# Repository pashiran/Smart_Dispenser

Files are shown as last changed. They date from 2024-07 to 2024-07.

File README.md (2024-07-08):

Smart Dispenser for MAKERS

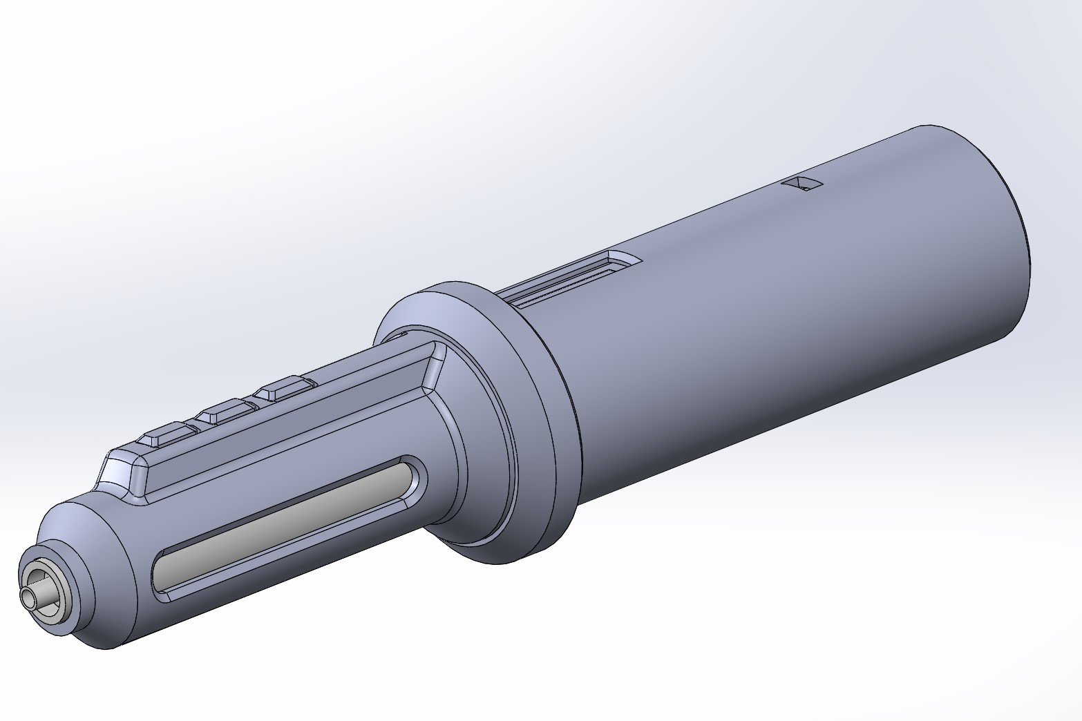
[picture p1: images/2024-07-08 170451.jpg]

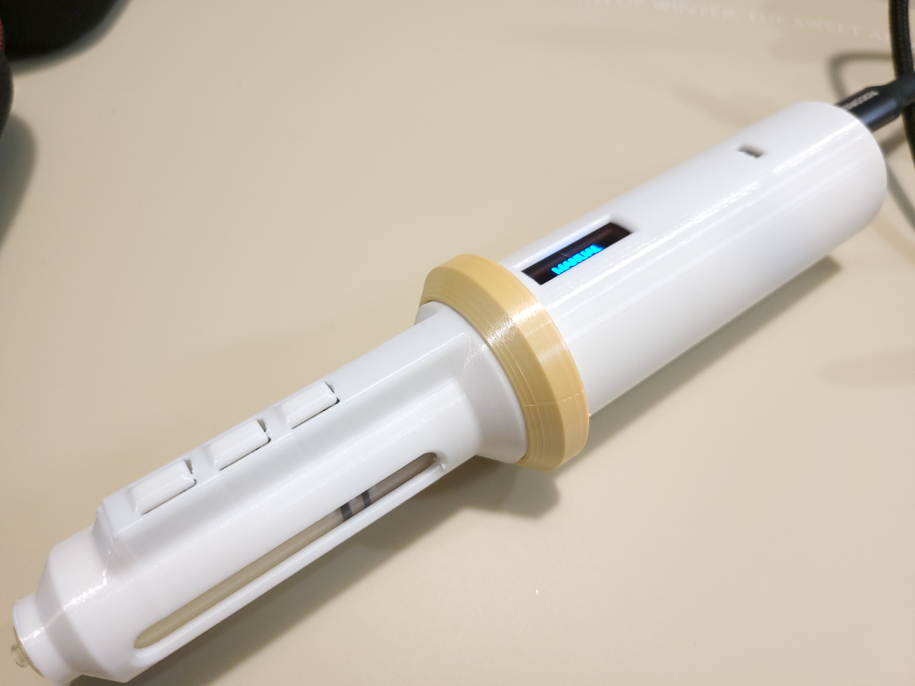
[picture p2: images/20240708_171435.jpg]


When you're building electronic circuits, some tools are so industrial that they're rarely useful for personal use. 
Instead of a giant pneumatic dispenser that sits on your desk, I created a USB-powered dispenser that fits in the palm of your hand. 

It took me a lot of time to build the hardware, electronics, and software all by myself. 
I'm not a professional programmer, so the software is waiting for other people to make it better.

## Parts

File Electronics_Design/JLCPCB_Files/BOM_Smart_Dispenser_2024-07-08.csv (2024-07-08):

ID | Name | Designator | Footprint | Quantity | Manufacturer Part | Manufacturer | Supplier | Supplier Part | Price
1 | TYPE-C-31-M-12 | USBC1 | USB-C_SMD-TYPE-C-31-M-12 | 1 | TYPE-C-31-M-12 | 韩国韩荣 | LCSC | C165948 | 0.163
2 | 5.1kΩ | R1 | R0805 | 1 | 0805W8F1002T5E | UNI-ROYAL(厚声) | LCSC | C17414 | 0.002
3 | 22pF | C1,C2 | C0805 | 2 | CL21C220JBANNNC | SAMSUNG(三星) | LCSC | C1804 | 0.01
4 | 4.7u | C10,C12,C16 | C0805 | 3
5 | 100nF | C11,C4,C3 | C0805 | 3 | C0805B104K500NT | TORCH(火炬) | LCSC | C476766 | 0.003
6 | 2.2u | C13 | C0805 | 1
7 | 1u | C14,C15 | C0805 | 2
8 | 0.1u | C17,C18 | C0805 | 2
9 | 100uF | C5 | CAP-D6.3×H5.5 | 1
10 | 4.7k | R6,R7,R8 | R0805 | 3
11 | 910k | R9 | R0805 | 1
12 | DRV8833PWP | U3 | TSSOP-16_L5.0-W4.4-P0.65-LS6.4-BL-EP | 1 | DRV8833PWPR | TI(德州仪器) | LCSC | C50506 | 0.639
13 | 1N5819 | U4 | SOD-123_L2.7-W1.6-LS3.7-FD | 1 | 1N5819W | HXY MOSFET(华轩阳电子) | LCSC | C5451628 | 0.006
14 | LM1117S-5.0 | U5 | SOT-223-3_L6.5-W3.4-P2.30-LS7.0-BR | 1 |  | HTC | LCSC | C126028 | 0.165
15 | 5.1kΩ | R10,R11 | R0805 | 2 | 0805W8F1001T5E | UNI-ROYAL(厚声) | LCSC | C17513 | 0.002
16 | 1kΩ | R12,R2,R3,R4 | R0805 | 4 | 0805W8F1001T5E | UNI-ROYAL(厚声) | LCSC | C17513 | 0.002
17 | LED-0603_R | LED1 | LED0603_RED | 1 | 19-217/R6C-AL1M2VY/3T | EVERLIGHT(台湾亿光) | LCSC | C72044 | 0.018
18 | TS-1101-C-W | RESET,SW1,SW2,SW3 | SW-SMD_L6.0-W3.3-LS8.0 | 4 | TS-1101-C-W | XKB Connectivity(中国星坤) | LCSC | C318938 | 0.033
19 | ATMEGA328P-AU | U1 | TQFP-32_L7.0-W7.0-P0.80-LS9.0-BL | 1 | ATMEGA328P-AU | MICROCHIP(美国微芯) | LCSC | C14877 | 2.131
20 | 0.1uF | C6 | C0805 | 1 | C0805B104K500NT | TORCH(火炬) | LCSC | C476766 | 0.003
21 | 10nF | C7 | C0805 | 1 | C0805B104K500NT | TORCH(火炬) | LCSC | C476766 | 0.003
22 | 2.2uF | C8 | C0805 | 1 | CL21A226MAYNNNE | SAMSUNG(三星) | LCSC | C602037 | 0.021
23 | 22uF | C9 | C0805 | 1 | CL21C222JBFNNNE | SAMSUNG(三星) | LCSC | C28260 | 0.029
24 | HDR-M-2.54_2x3 | J1 | HDR-M-2.54_2X3 | 1 |  |  | LCSC | C65114 | 0.029
25 | HDR-M-2.54_1x6 | J2 | HDR-M-2.54_1X6 | 1 |  |  | LCSC | C190819 | 0.029
26 | SC662K-3.3V | LDO1 | SOT-23-3_L2.9-W1.3-P1.90-LS2.4-BR | 1 | SC662K-3.3V | FM(富满) | LCSC | C83932 | 0.034
27 | CH340K | U2 | ESOP-10_L4.9-W3.9-P1.00-LS6.2-BL-EP | 1 | CH340K | WCH(南京沁恒) | LCSC | C968586 | 0.629
28 | SSD1306_OLED | U6 | 0.91"OLED_FOLD | 1
29 | 16MHZ | Y1 | X3-SMD-3.6X1.3X0.8MM | 1 | CSTCE16M00G55-RO |  | SeeedStudio | 306010053
30 | 10kΩ | R5 | R0805 | 1 | 0805W8F1002T5E | UNI-ROYAL(厚声) | LCSC | C17414 | 0.002

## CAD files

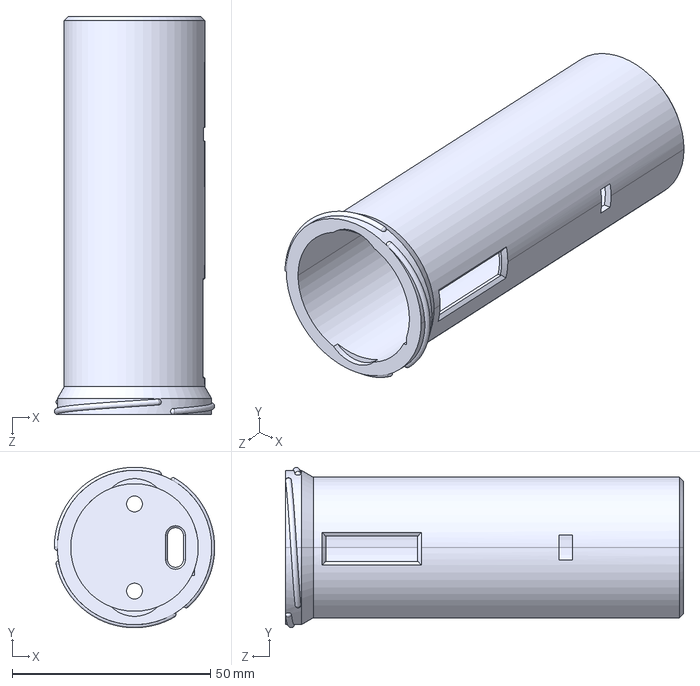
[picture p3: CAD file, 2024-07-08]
3D_Cad/STEP/Main_Body_Cover.STEP
40.5 x 40.5 x 100.5 mm

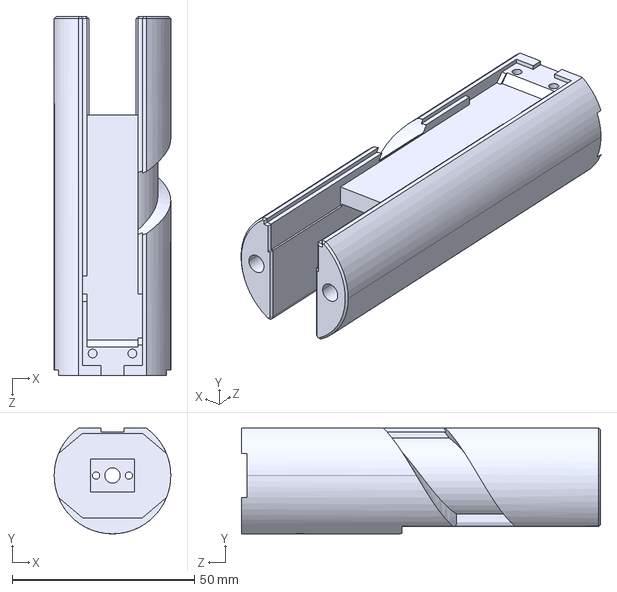
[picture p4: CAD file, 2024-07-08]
3D_Cad/STEP/Main_Body.STEP
32.0 x 29.0 x 98.5 mm

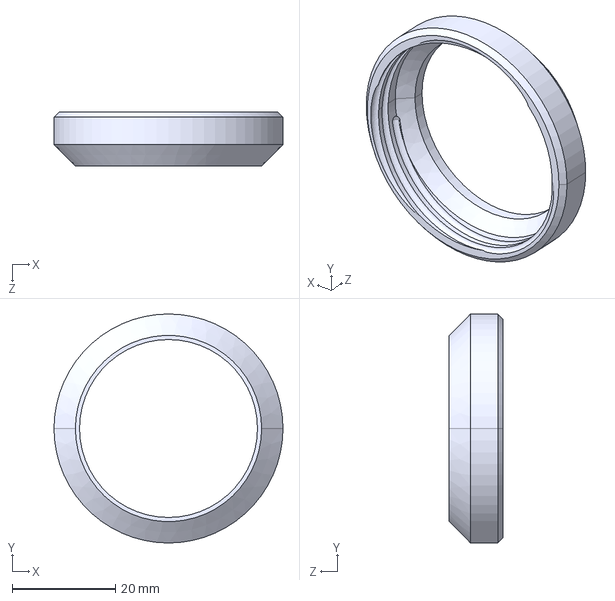
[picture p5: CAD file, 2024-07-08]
3D_Cad/STEP/Joint_Handle.STEP
44.4 x 44.4 x 10.5 mm

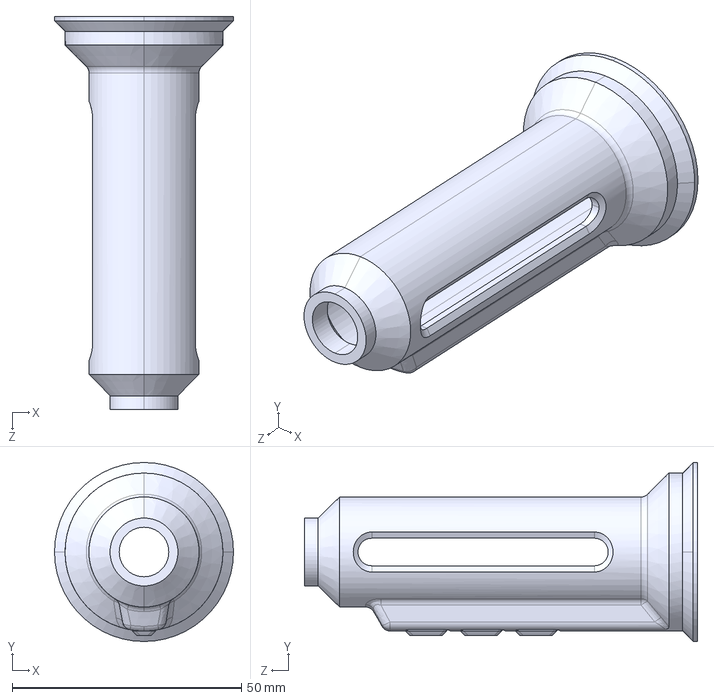
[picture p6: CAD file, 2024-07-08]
3D_Cad/STEP/Front_Body.STEP
39.0 x 39.0 x 85.7 mm

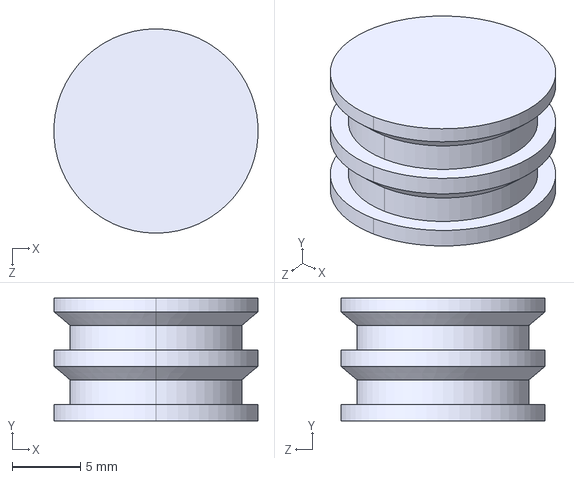
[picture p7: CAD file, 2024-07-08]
3D_Cad/STEP/Pusher_A.STEP
15.0 x 9.00 x 15.0 mm

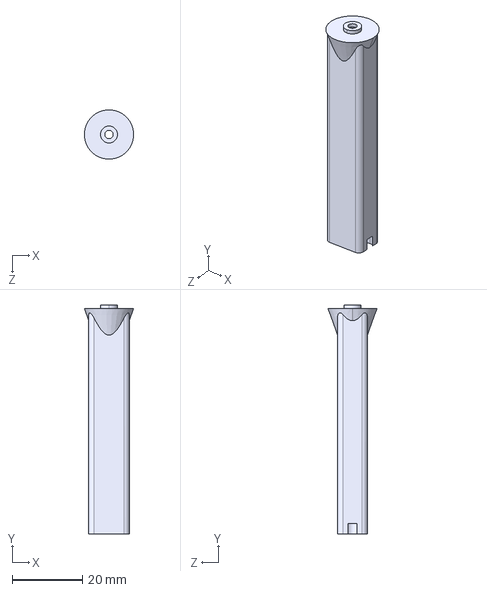
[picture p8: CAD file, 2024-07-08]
3D_Cad/STEP/Pusher_B.STEP
14.0 x 65.0 x 14.0 mm

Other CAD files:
3D_Cad/STL/Front_Body.STL
3D_Cad/STL/Joint_Handle.STL
3D_Cad/STL/Main_Body.STL
3D_Cad/STL/Main_Body_Cover.STL
3D_Cad/STL/Pusher_A.STL
3D_Cad/STL/Pusher_B.STL

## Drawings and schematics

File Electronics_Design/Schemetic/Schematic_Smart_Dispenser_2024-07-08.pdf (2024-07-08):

## Input A1: Voltage

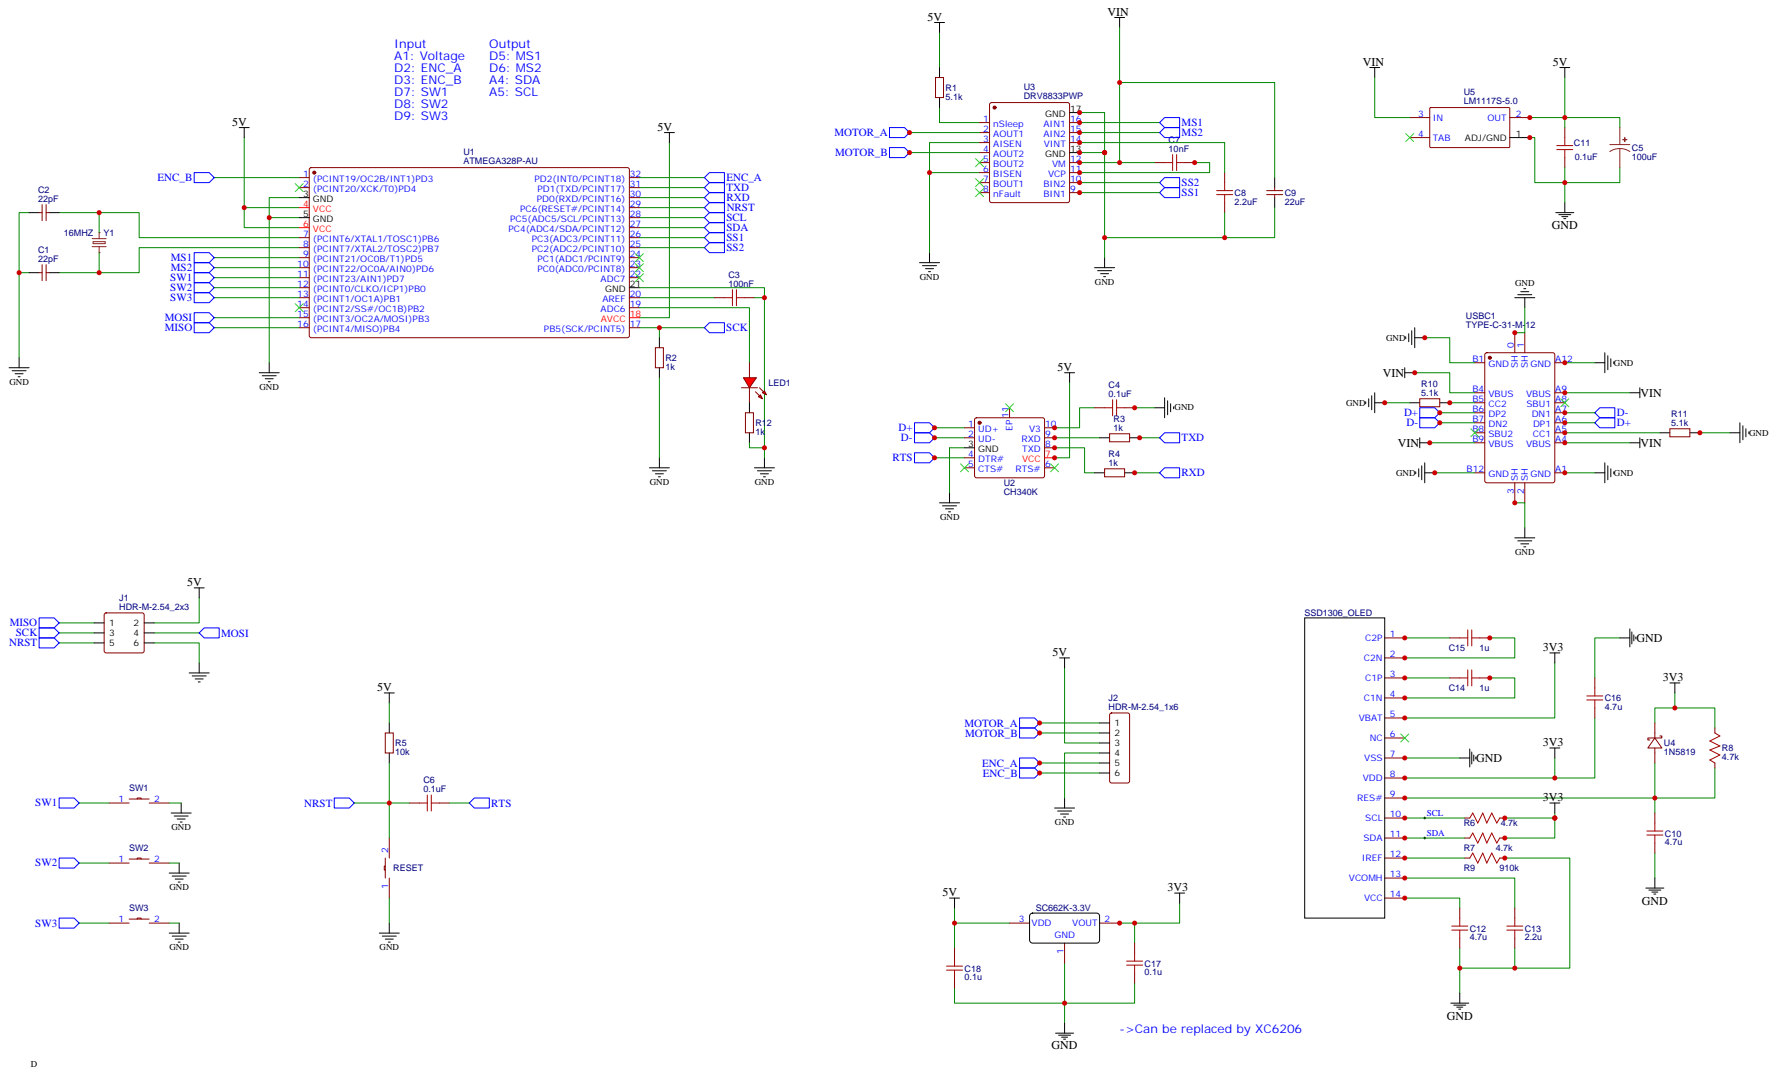
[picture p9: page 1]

->Can be replaced by XC6206

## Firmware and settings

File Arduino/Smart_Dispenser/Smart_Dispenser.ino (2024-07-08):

#include "U8glib.h"
#include "EEPROM.h"
#include "Encoder.h"  // https://github.com/PaulStoffregen/Encoder


// 핀 정의
#define encoderA 2  // pin of motor encoder - interrupt of arduino nano
#define encoderB 3  // pin of motor encoder - interrupt of arduino nano
#define up_Pin 7    // Up switch
#define sel_Pin 8   // Select switch
#define down_Pin 9  // Down switch
//#define limit_Pin 10  // Limit sensor

#define AIN_Pin_1 5  // drv8833 signal 1 : PWM
#define AIN_Pin_2 6  // drv8833 signal 2 : PWM

// 전역 변수
long newPosition;
long oldPosition;    // encoder position
boolean direction;   // true = cylinder advance, false = cylinder retraction
int min_error = 30;  // encoder difference less than this number will be ignored

long currentPos;  // cylinder first(=current) position
long targetPos;   // cylinder position to move
long difference;  // difference of currentPos and targetPos

boolean up_Flag = false, select_Flag = false, down_Flag = false;  // switch flag

byte address;  // EEPROM address (0:stage, 1:Extrusion, 2:Retraction, 3:Speed)
byte Stage = 0, previous_Stage = 0;  // 0 = manual, 1 = auto, 2 = PnP, 4 = Setup
byte setup_Stage = 0;        // setup stage, 0 = extrusion, 1 = retraction, 2 = speed
byte Extrusion;              // extrusion set amount.(min:0 / max:100), maximum extrusion moves the cylinder 5mm
byte Retraction;             // retraction set amount.(min:0 / max:10), maximum retraction moves the cylinder 1mm
int Speed;                   // speed of motor(min: -255 / max :255), minus means direction
byte Backlash;               // backlash
float Pitch = 0.4;           // pitch of M4 bolt.
int gearRatio = 50;          // gear ratio of geared motor.
byte X, Y;                   // coordinate of OLED screen

unsigned long current_Millis, previous_Millis = 0;  // Time variable to check the time the switch is pressed
unsigned long pressed_Time = 500;  // Time-based variable. If it is longer than this, it is considered as a LONG press.


long initialPosition;            // PnP 모드에서 엔코더의 현재 위치 저장 변수


U8GLIB_SSD1306_128X32 u8g(U8G_I2C_OPT_FAST);  // I2C / TWI
Encoder myEncoder(encoderA, encoderB);

void setup() {
  pinMode(up_Pin, INPUT_PULLUP);
  pinMode(sel_Pin, INPUT_PULLUP);
  pinMode(down_Pin, INPUT_PULLUP);
  pinMode(encoderA, INPUT_PULLUP);
  pinMode(encoderB, INPUT_PULLUP);

  pinMode(AIN_Pin_1, OUTPUT);
  pinMode(AIN_Pin_2, OUTPUT);

  u8g.setFont(u8g_font_helvB10);

  u8g.setFontRefHeightExtendedText();
  u8g.setDefaultForegroundColor();
  u8g.setFontPosTop();

  Serial.begin(9600);
  Serial.println("OK");

  if (EEPROM.read(0) == 255) {  // if there are no saved settings
    Extrusion = 10;             // use default value
    Retraction = 1;
    Speed = 255;
    // 초기화 완료 표시를 위해 임의의 값을 EEPROM의 첫 번째 위치에 기록
    EEPROM.write(0, 0);
    EEPROM.write(1, Extrusion);
    EEPROM.write(2, Retraction);
    EEPROM.write(3, Speed);
  } else {
    Extrusion = EEPROM.read(1);
    Retraction = EEPROM.read(2);
    Speed = EEPROM.read(3);
  }

  draw();
}

void loop() {
  newPosition = myEncoder.read();
  current_Millis = millis();

  // Stage에 따른 동작 처리
  switch (Stage) {
    case 0:  // manual stage
      // 스위치 상태 읽기
      if(digitalRead(up_Pin) == LOW) {
        digitalWrite(AIN_Pin_1, Speed);
        digitalWrite(AIN_Pin_2, LOW);
      }
      if(digitalRead(down_Pin) == LOW) {
        digitalWrite(AIN_Pin_1, LOW);
        digitalWrite(AIN_Pin_2, Speed);
      }
      if((digitalRead(up_Pin) == HIGH) && (digitalRead(down_Pin) == HIGH)){
        stopMotor();
      }
      
      // sel 스위치 처리 함수 호출
      handleSelSwitch();
      break;

    case 1:  // auto stage
      // up 스위치를 누르면 - extrusion 거리 만큼 전진한 뒤 retraction 거리만큼 후진하고 멈춘다.
      if (!up_Flag && digitalRead(up_Pin) == LOW) {
        up_Flag = true;
      } else if (up_Flag && digitalRead(up_Pin) == HIGH) {
        up_Flag = false;
        moveMotor(Extrusion);
        moveMotor(-Retraction);
        stopMotor();
      }

      // down 스위치를 눌렀다 떼면 - extrusion 거리 만큼 후진하고 멈춘다.
      if (!down_Flag && digitalRead(down_Pin) == LOW) {
        down_Flag = true;
      } else if (down_Flag && digitalRead(down_Pin) == HIGH) {
        down_Flag = false;
        moveMotor(-Extrusion);
        stopMotor();
      }

      // sel 스위치를 처리 함수 호출
      handleSelSwitch();
      break;

    case 2:  // Pick and Place stage
      // up 스위치를 누르면 - 스위치를 누른 동안 계속 후진하다가 스위치를 떼면 다시 현재 위치까지 돌아오고 멈춘다.
      if (!up_Flag && digitalRead(up_Pin) == LOW) {
        up_Flag = true;
        initialPosition = myEncoder.read();  // 현재 위치 저장
      } else if (up_Flag && digitalRead(up_Pin) == LOW) {
        // 스위치가 눌린 동안 계속 후진
        digitalWrite(AIN_Pin_1, LOW);
        analogWrite(AIN_Pin_2, Speed);
      } else if (up_Flag && digitalRead(up_Pin) == HIGH) {
        // 스위치가 떼지면 최대 속도로 기존의 위치로 돌아옴
        up_Flag = false;
        long target = initialPosition;
        while (newPosition != target) {
          newPosition = myEncoder.read();
          if (newPosition < target) {
            analogWrite(AIN_Pin_1, 255);  // 최대 속도로 전진
            digitalWrite(AIN_Pin_2, LOW);
          } else {
            digitalWrite(AIN_Pin_1, LOW);
            analogWrite(AIN_Pin_2, 255);  // 최대 속도로 후진
          }
        }
        stopMotor();
      }

      // sel 스위치를 처리 함수 호출
      handleSelSwitch();
      break;

    case 4:  // setup stage
      // up 스위치 상태 읽기
      if (!up_Flag && digitalRead(up_Pin) == LOW) {
        up_Flag = true;
        if (setup_Stage == 0 && Extrusion < 100) {
          Extrusion++;
          draw(); // 화면 업데이트
        } else if (setup_Stage == 1 && Retraction < 10) {
          Retraction++;
          draw(); // 화면 업데이트
        } else if (setup_Stage == 2) {
          if (Speed < 255) {
            Speed += 26;  // 0~255 범위에서 10단계로 변하기 위해
            if (Speed > 255) Speed = 255;
            draw(); // 화면 업데이트
          }
        }
      } else if (up_Flag && digitalRead(up_Pin) == HIGH) {
        up_Flag = false;
      }

      // down 스위치 상태 읽기
      if (!down_Flag && digitalRead(down_Pin) == LOW) {
        down_Flag = true;
        if (setup_Stage == 0 && Extrusion > 0) {
          Extrusion--;
          draw(); // 화면 업데이트
        } else if (setup_Stage == 1 && Retraction > 0) {
          Retraction--;
          draw(); // 화면 업데이트
        } else if (setup_Stage == 2) {
          if (Speed > 0) {
            Speed -= 26;  // 0~255 범위에서 10단계로 변하기 위해
            if (Speed < 0) Speed = 0;
            draw(); // 화면 업데이트
          }
        }
      } else if (down_Flag && digitalRead(down_Pin) == HIGH) {
        down_Flag = false;
      }

      // sel 스위치를 처리 함수 호출
      handleSelSwitch();
      break;

  }

  // 위치 변경 시 OLED 화면 업데이트
  if (newPosition != oldPosition) {
    oldPosition = newPosition;
    draw();
  }
}

void stopMotor() {
    digitalWrite(AIN_Pin_1, HIGH);
  digitalWrite(AIN_Pin_2, HIGH);
}

// 모터를 지정된 거리만큼 이동시키는 함수
void moveMotor(int distance) {
  // 이동할 거리를 엔코더 신호 수로 변환
  int counts = (distance * 12 * gearRatio) / Pitch;
  long target = newPosition + counts;

  while (newPosition != target) {
    newPosition = myEncoder.read();
    if (counts > 0) {
      digitalWrite(AIN_Pin_1, Speed);
      digitalWrite(AIN_Pin_2, LOW);
    } else {
      digitalWrite(AIN_Pin_1, LOW);
      digitalWrite(AIN_Pin_2, Speed);
    }
  }
}

// sel 스위치 입력 처리 함수
void handleSelSwitch() {
  if (!select_Flag && digitalRead(sel_Pin) == LOW) {
    select_Flag = true;
    previous_Millis = current_Millis;  // 버튼을 누른 시간 저장
  } else if (select_Flag && digitalRead(sel_Pin) == HIGH) {
    unsigned long pressDuration = current_Millis - previous_Millis;

    if (pressDuration < pressed_Time) {
      // Short press: Stage 변경 또는 setup_Stage 순환
      if (Stage == 4) {
        setup_Stage = (setup_Stage + 1) % 3; // setup stage 순환
      } else {
        Stage = (Stage + 1) % 3; // 0, 1, 2 순환
      }
    } else {
      // Long press: Setup stage로 전환 또는 이전 Stage로 복귀
      if (Stage == 4) {
        // Setup stage에서 벗어날 때 EEPROM에 값 저장
        EEPROM.update(1, Extrusion);
        EEPROM.update(2, Retraction);
        EEPROM.update(3, Speed);
        
        Stage = previous_Stage;  // 이전 Stage로 복귀
      } else {
        previous_Stage = Stage;  // 현재 Stage 저장
        Stage = 4;               // Setup stage로 전환
      }
    }
    draw();
    select_Flag = false;
  }
}


void draw() {
  u8g.firstPage();
  do {
    int strWidth;
    int strHeight = u8g.getFontAscent() - u8g.getFontDescent();
    int x, y;

    switch (Stage) {
      case 0:  // manual stage, motor runs when up/down switch pressed.
        strWidth = u8g.getStrWidth("MANUAL");
        x = (128 - strWidth) / 2;  // 화면 가로 중앙
        y = (32 - strHeight) / 2;  // 화면 세로 중앙
        u8g.drawStr(x, y, "MANUAL");
        break;

      case 1:  // auto stage, The motor runs for a set amount.
        strWidth = u8g.getStrWidth("AUTO");
        x = (128 - strWidth) / 2;  // 화면 가로 중앙
        y = (32 - strHeight) / 2;  // 화면 세로 중앙
        u8g.drawStr(x, y, "AUTO");
        break;

      case 2:  // Pick and Place stage, motor runs forward when UP switch pressed and backward when released.
        strWidth = u8g.getStrWidth("PnP");
        x = (128 - strWidth) / 2;  // 화면 가로 중앙
        y = (32 - strHeight) / 2;  // 화면 세로 중앙
        u8g.drawStr(x, y, "PnP");
        break;

      case 4:  // Setup stage, you can adjust settings here.
        switch (setup_Stage) {  // 0 = extrusion, 1 = retraction, 2 = speed
          case 0:
            {
              String extrusionText = "Extrusion: " + String(Extrusion);
              strWidth = u8g.getStrWidth(extrusionText.c_str());
              x = (128 - strWidth) / 2;  // 화면 가로 중앙
              y = 0;  // 화면 세로 제일 위
              u8g.drawStr(x, y, extrusionText.c_str());
            }
            u8g.drawFrame(0, 17, 128, 14);
            u8g.drawBox(0, 17, Extrusion, 14);
            break;
          case 1:
            {
              String retractionText = "Retraction: " + String(Retraction);
              strWidth = u8g.getStrWidth(retractionText.c_str());
              x = (128 - strWidth) / 2;  // 화면 가로 중앙
              y = 0;  // 화면 세로 제일 위
              u8g.drawStr(x, y, retractionText.c_str());
            }
            u8g.drawFrame(0, 17, 128, 14);
            u8g.drawBox(0, 17, Retraction, 14);
            break;
          case 2:
            {
              int mappedSpeed = map(Speed, 0, 255, 1, 10);  // Speed 값을 1~10으로 매핑
              String speedText = "Speed: " + String(mappedSpeed);
              strWidth = u8g.getStrWidth(speedText.c_str());
              x = (128 - strWidth) / 2;  // 화면 가로 중앙
              y = 0;  // 화면 세로 제일 위
              u8g.drawStr(x, y, speedText.c_str());
            }
            u8g.drawFrame(0, 17, 128, 14);
            u8g.drawBox(0, 17, map(Speed, 0, 255, 0, 128), 14);  // Speed 값을 0~128으로 매핑하여 막대그래프로 표시
            break;
        }
        break;
    }
  } while (u8g.nextPage());
}
